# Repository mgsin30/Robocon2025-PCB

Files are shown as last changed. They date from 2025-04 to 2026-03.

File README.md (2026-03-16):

# Robocon2025-PCB
高専ロボコン2025のために開発した基板 <br>
各基板のファームウェアは [こちら](https://github.com/mgsin30/Robocon2025-Firmware)

## CAN Bus Hub
各基板を CAN バスで接続するためのハブ基板

## Converter Board
サーボモーターや LED テープなどのために電源電圧を降圧する基板

## GPIO Board
リミットスイッチやジャイロセンサー、その他 GPIO を使うための基板

## Motor Driver
ブラシ付きモーター用のモータードライバー

## Power Board
電源電圧の監視や非常停止の管理などを行う電源基板

## PWM Board
サーボモーターなどを使うための基板

## Remote Emergency Stop Board (TX)
遠隔非常停止の送信側基板

## Remote Emergency Stop Board (RX)
遠隔非常停止の受信側基板

## RoboMaster Board
ロボマスモーターを使うための基板

## Solenoid Driver
ソレノイドや電磁弁などを使うための基板

## USB-CAN Board
USB と CAN を変換する基板

## XT30 Hub
XT30 コネクタのハブ基板

## XT60 Hub
XT60 コネクタのハブ基板

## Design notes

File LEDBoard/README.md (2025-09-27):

# LED Board

LEDテープ WS2812B を光らせるための基板

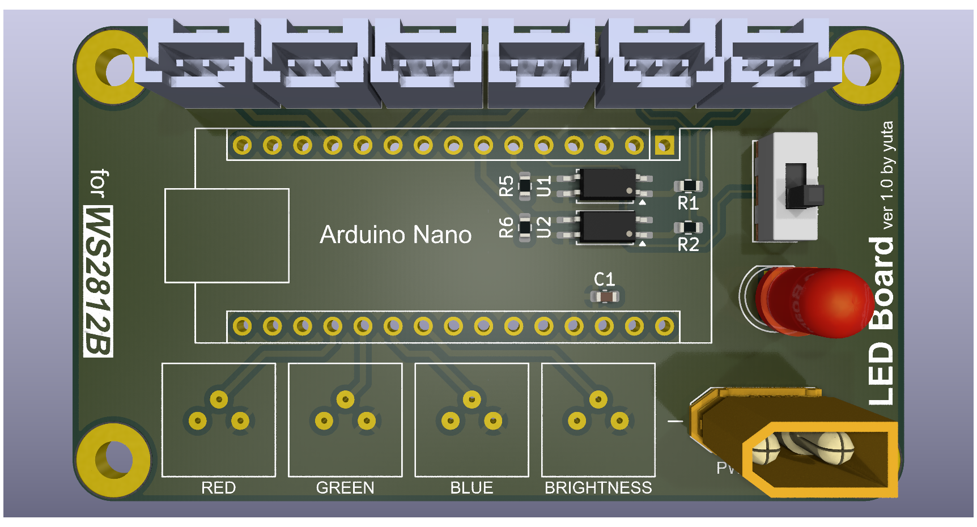
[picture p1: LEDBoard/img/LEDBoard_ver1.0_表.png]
表面

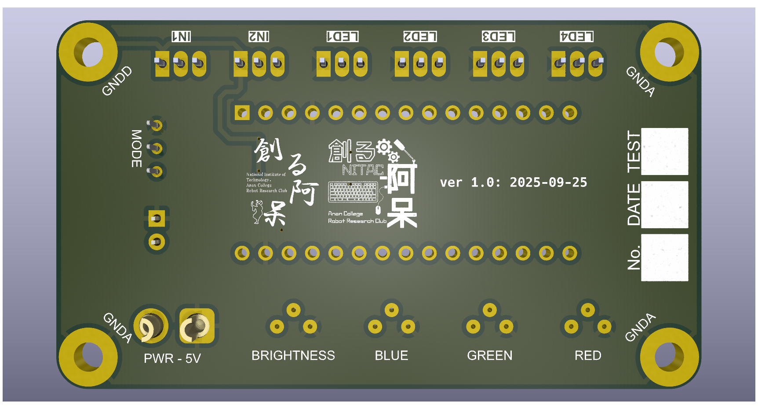
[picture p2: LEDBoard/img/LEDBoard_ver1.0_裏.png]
裏面


## 変更履歴

### ver1.0 (完成日：2025/09/25)
- 初回完成

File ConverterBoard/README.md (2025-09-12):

# Converter Board

電源電圧を各電圧に降圧するための基板

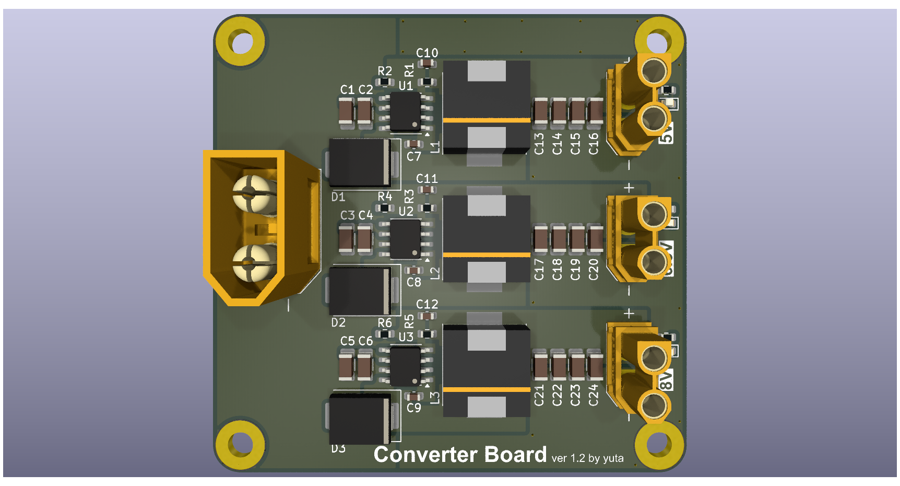
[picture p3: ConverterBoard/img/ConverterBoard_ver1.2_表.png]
表面

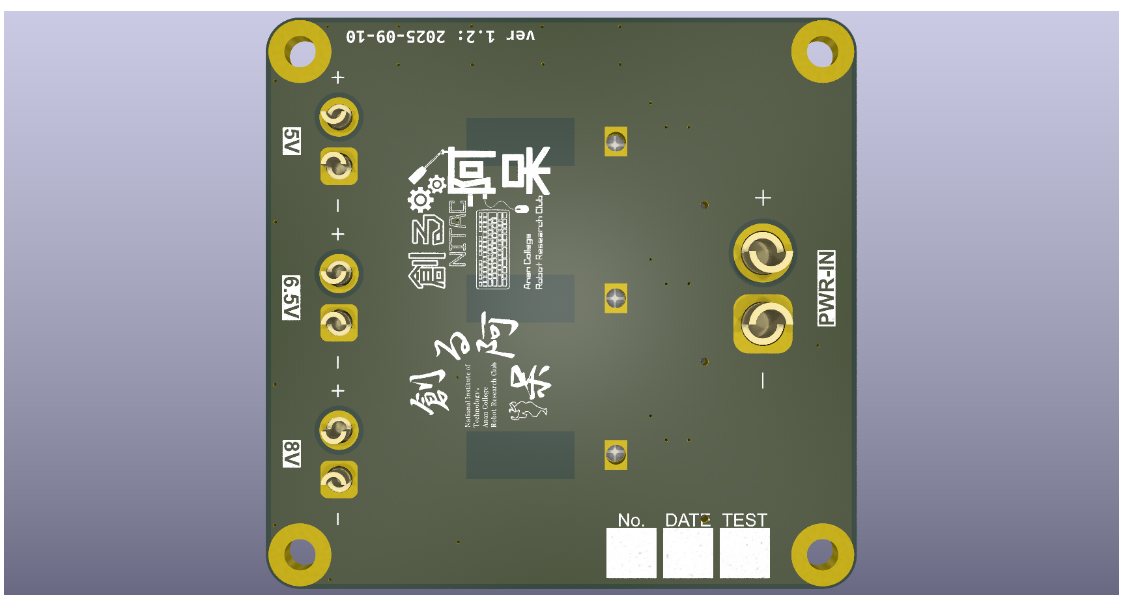
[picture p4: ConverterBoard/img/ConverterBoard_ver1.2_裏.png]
裏面


## 変更履歴

### ver1.0 (完成日：2025/05/31)
- 初回完成

### ver1.1 (完成日：2025/06/17)
- D1, D2, D3 のフットプリントを修正
- U1, U2, U3 のフットプリントを修正

### ver1.2 (完成日：2025/09/10)
- 12V出力を8V出力に変更
- 電源確認用LEDを追加
- 裏面のロゴの位置を微調整

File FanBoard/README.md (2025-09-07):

# Fan Board

空冷ファン用基板

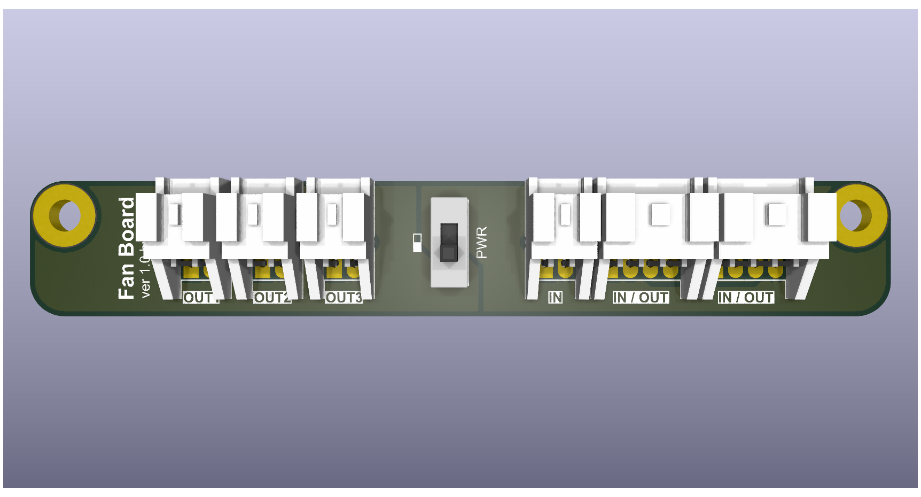
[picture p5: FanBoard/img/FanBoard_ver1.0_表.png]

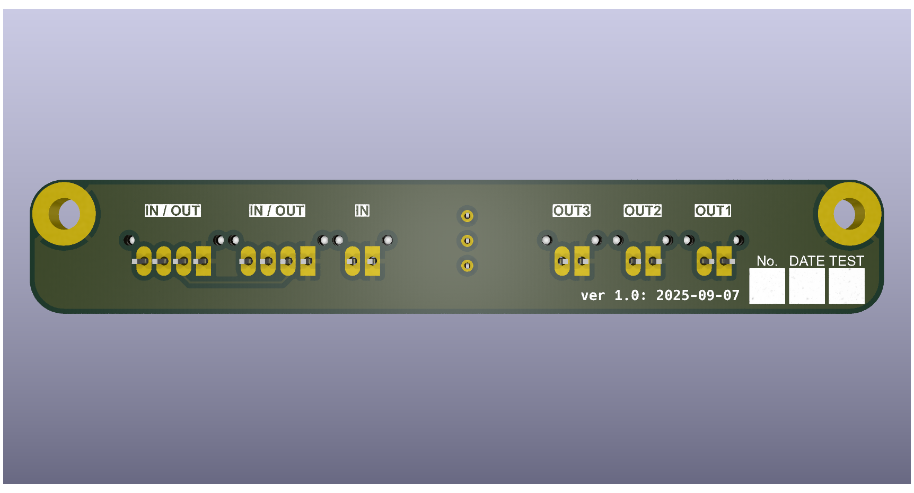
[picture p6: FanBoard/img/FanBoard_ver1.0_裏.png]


## 変更履歴

### ver1.0 (完成日：2025/09/07)
- 初回完成

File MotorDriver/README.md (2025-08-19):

# Motor Driver

ブラシ付きモーター用のモータードライバー

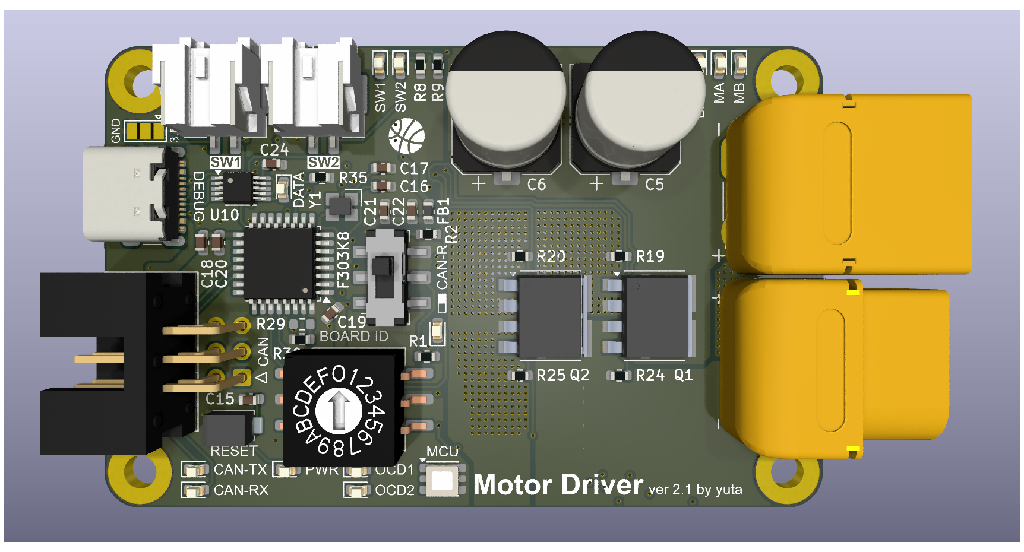
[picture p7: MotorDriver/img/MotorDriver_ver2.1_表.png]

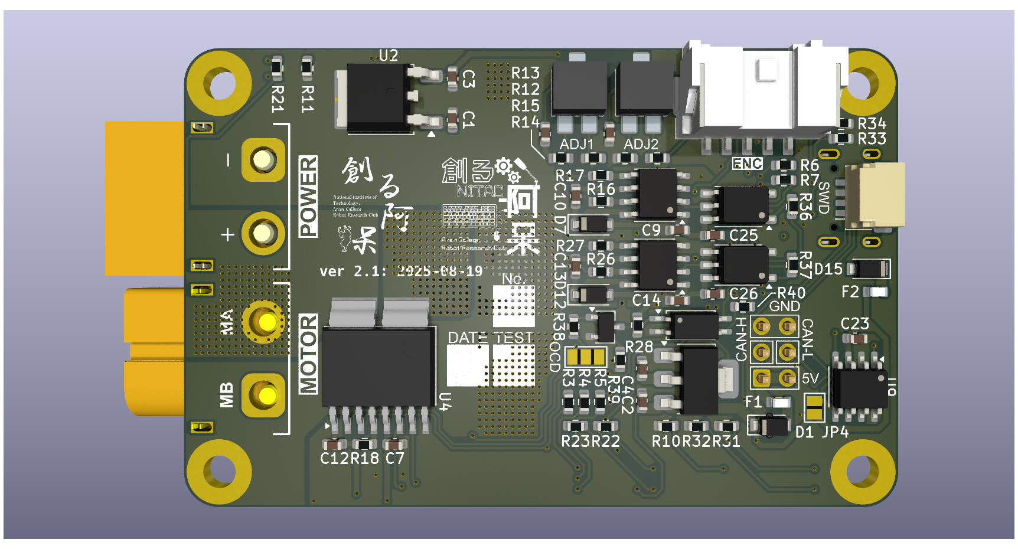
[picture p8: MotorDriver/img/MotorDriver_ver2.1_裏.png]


## 変更履歴

### ver1.0 (発注日：2025/02/24)
- 初回完成

### ver2.0 (完成日：2025/07/11)
- 小型化
- マイコンを搭載
- 他の基板に合わせて仕様を変更

### ver2.1 (完成日：2025/08/19)
- エンコーダー用のピンを変更
- MOSFETのフットプリントを修正
- C23のシルクを追加

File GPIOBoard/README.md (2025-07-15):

# GPIO Board

リミットスイッチや IMU を接続したり、GPIO を利用したりするための基板

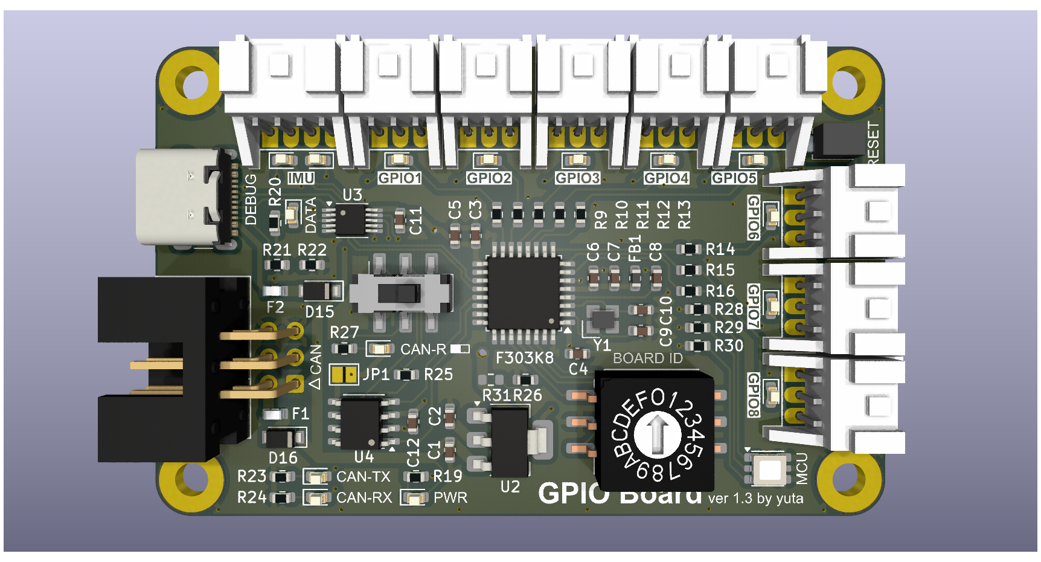
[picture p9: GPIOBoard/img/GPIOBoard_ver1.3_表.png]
表面

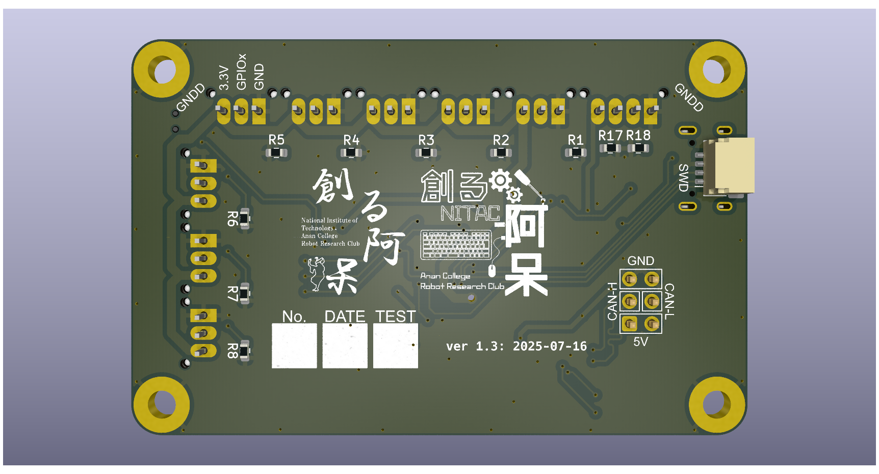
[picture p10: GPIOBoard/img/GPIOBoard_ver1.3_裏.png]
裏面


## 変更履歴

### ver1.0 (発注日：2025/03/10)
- 初回完成

### ver1.1 (発注日：2025/04/12)
- 三端子レギュレーターの型番を変更
- ショットキーバリアダイオードの型番を変更
- 各LEDの型番を変更
- 電源確認用LEDの場所を変更
- RGBLEDを追加
- 終端抵抗接続用スイッチの型番を変更
- 終端抵抗接続確認用のLEDを追加
- シルクを微調整
- 水晶発振子のフットプリントを修正

### ver1.2 (発注日：2025/07/01)
- USB-Cコネクタの位置を微調整
- 基板下部の取付穴を通常の穴に変更

### ver1.3 (発注日：2025/07/16)
- USBのCCピンが未配線だったのを修正
- フットプリントを更新

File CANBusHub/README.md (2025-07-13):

# CAN Bus Hub

各基板と CANバス を接続する基板

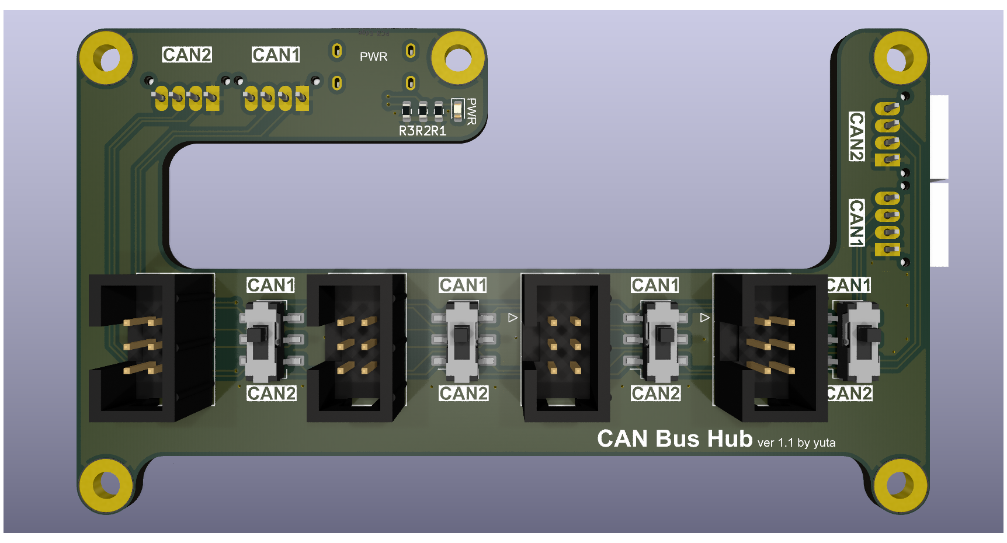
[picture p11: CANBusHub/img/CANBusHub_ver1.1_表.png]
表面

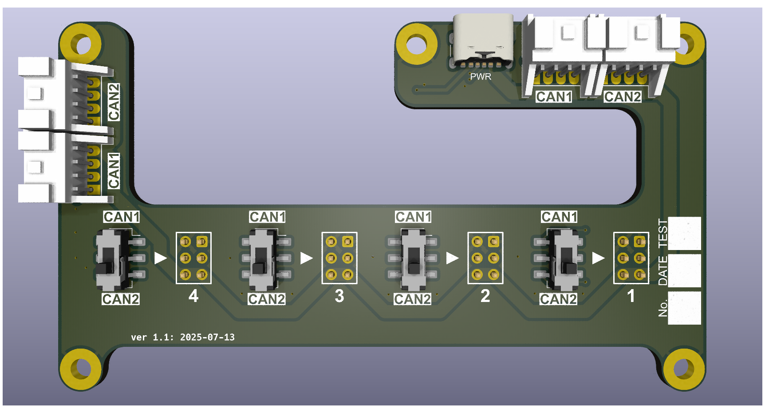
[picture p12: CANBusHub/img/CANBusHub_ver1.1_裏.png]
裏面


## 変更履歴

### ver1.0 (完成日：2025/05/30)
- 初回完成

### ver1.1 (完成日：2025/07/13)
- 基板接続用コネクタとCANバス切替用スイッチの位置を変更
- CAN用コネクタの位置を変更
- 裏面にシルクスクリーンを追加

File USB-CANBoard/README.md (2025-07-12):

# USB-CAN Board

USB と CAN の変換基板

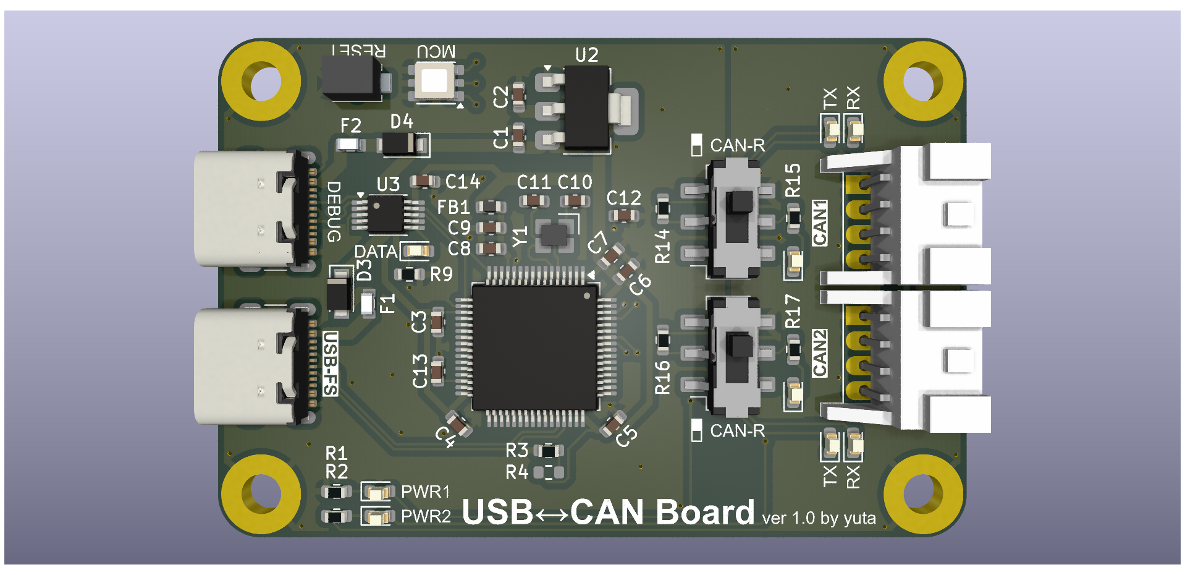
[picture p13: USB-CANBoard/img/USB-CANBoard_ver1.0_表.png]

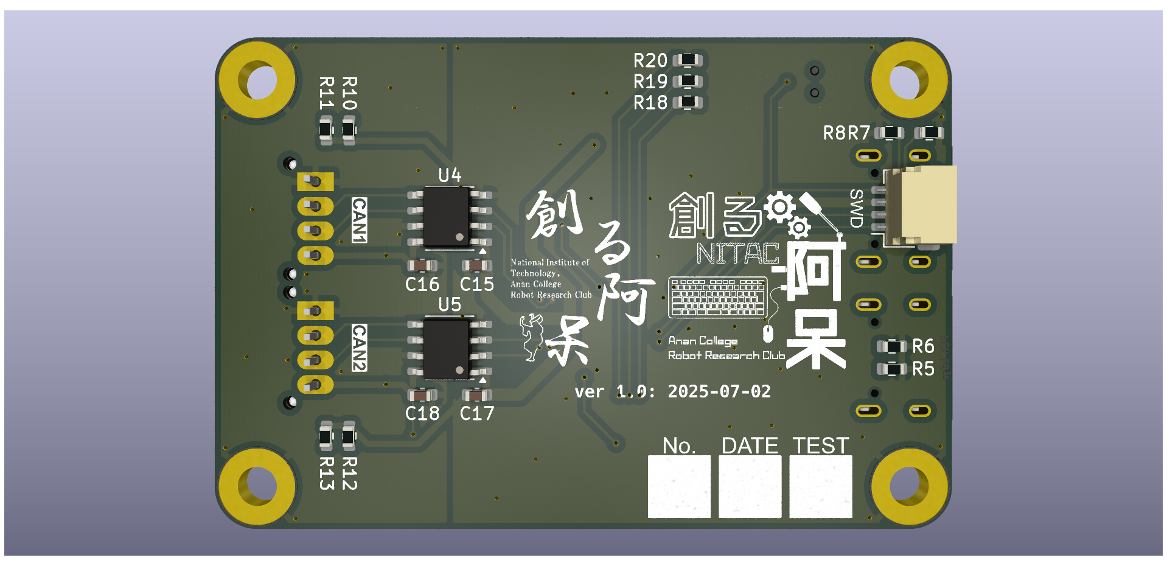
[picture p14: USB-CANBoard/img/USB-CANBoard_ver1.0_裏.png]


## 変更履歴

### ver1.0 (完成日：2025/07/02)
- 初回完成

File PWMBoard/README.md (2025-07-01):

# PWM Board

PWM を出力し、サーボモーターや ESC、LEDテープを接続するための基板

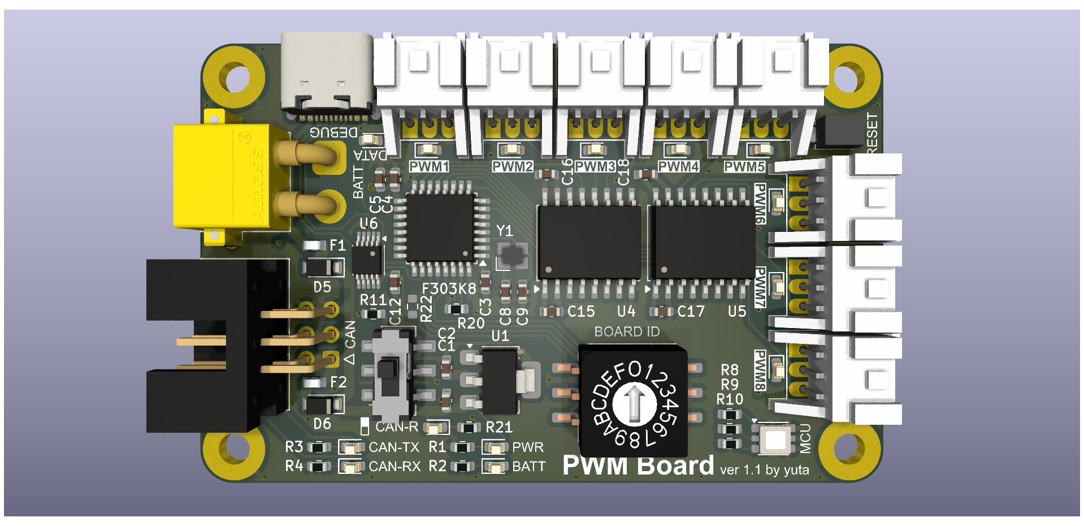
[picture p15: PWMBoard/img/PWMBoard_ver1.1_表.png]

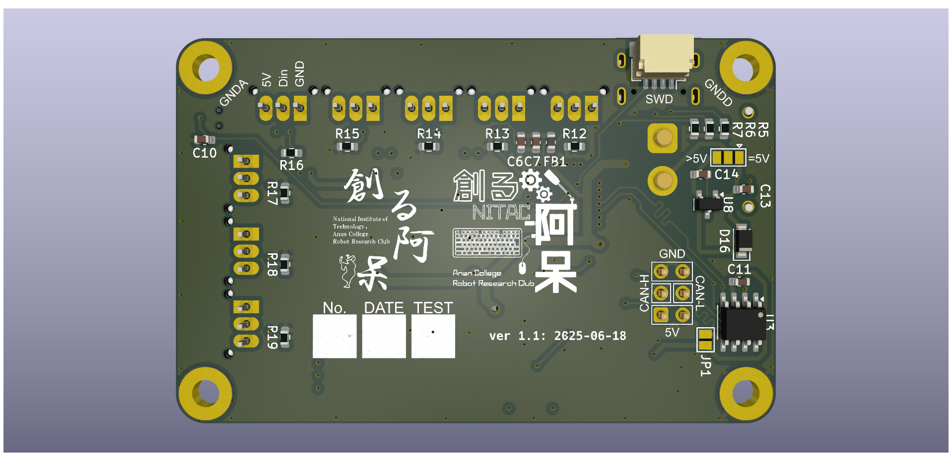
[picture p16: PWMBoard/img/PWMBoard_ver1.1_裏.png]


## 変更履歴

### ver1.0 (発注日：2025/04/12)
- 初回完成

### ver1.1 (完成日：2025/06/18)
- 電源コネクタの接続が逆になっていたのを修正
- 基板下部の取付穴を通常の穴に変更

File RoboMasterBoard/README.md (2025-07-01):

# RoboMaster Board

ロボマスモーターを制御するための基板

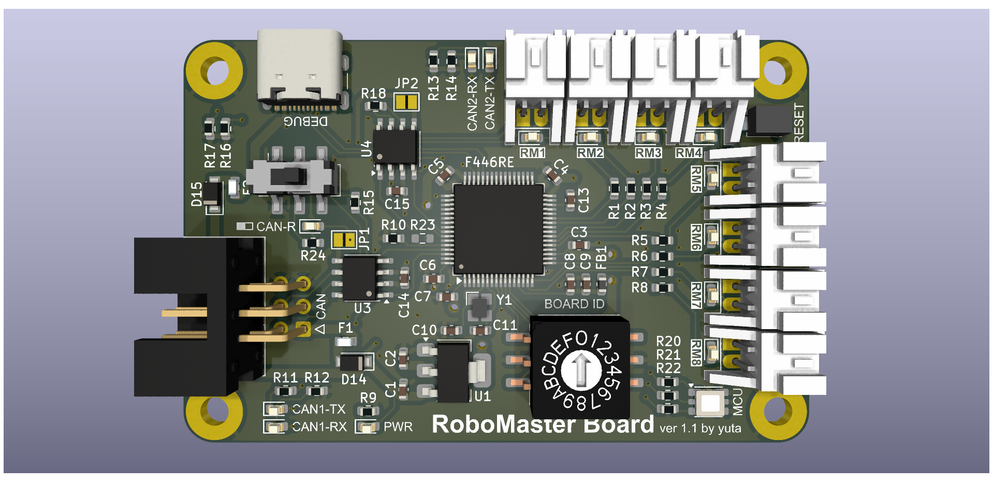
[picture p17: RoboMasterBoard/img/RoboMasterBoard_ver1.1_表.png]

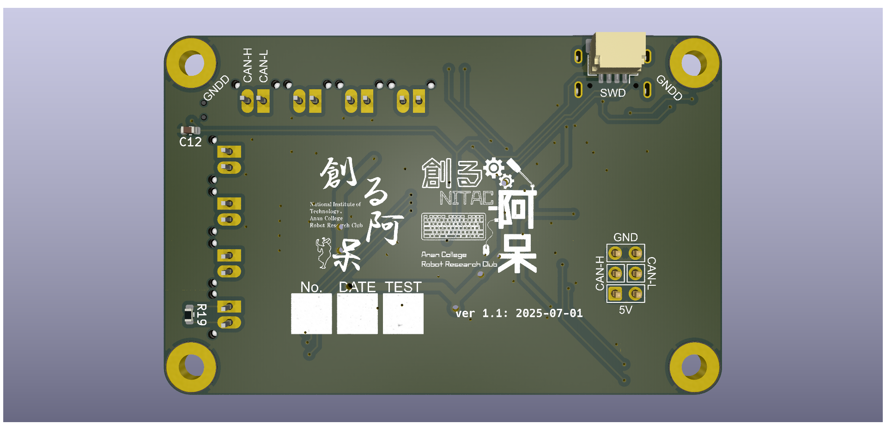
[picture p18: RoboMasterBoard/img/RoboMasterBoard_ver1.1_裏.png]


## 変更履歴

### ver1.0 (発注日：2025/04/12)
- 初回完成

### ver1.1 (発注日：2025/07/01)
- 未接続の箇所を修正
- 水晶発振子の型番を変更
- U2 のシルクの向きを変更
- 基板下部の取付穴を通常の穴に変更

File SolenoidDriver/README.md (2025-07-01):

# Solenoid Driver

ソレノイドやソレノイドバルブを制御するための基板

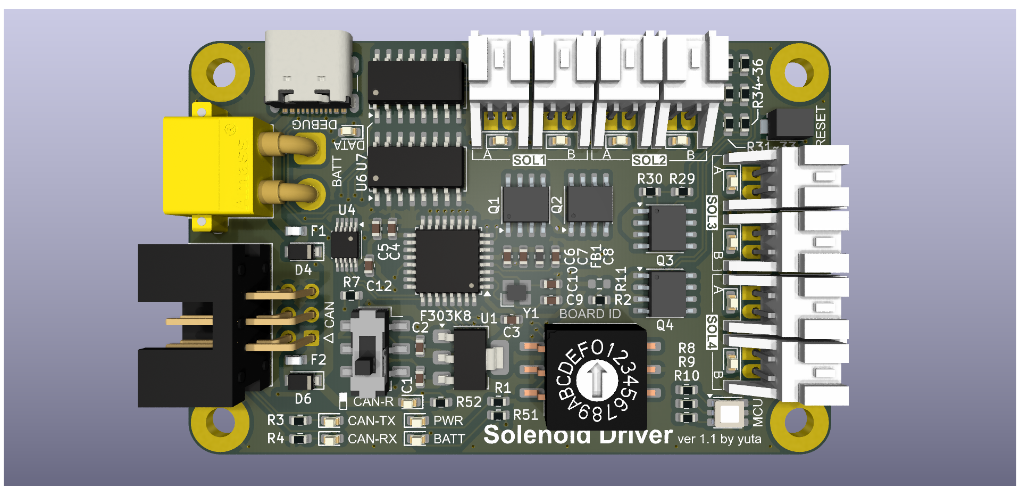
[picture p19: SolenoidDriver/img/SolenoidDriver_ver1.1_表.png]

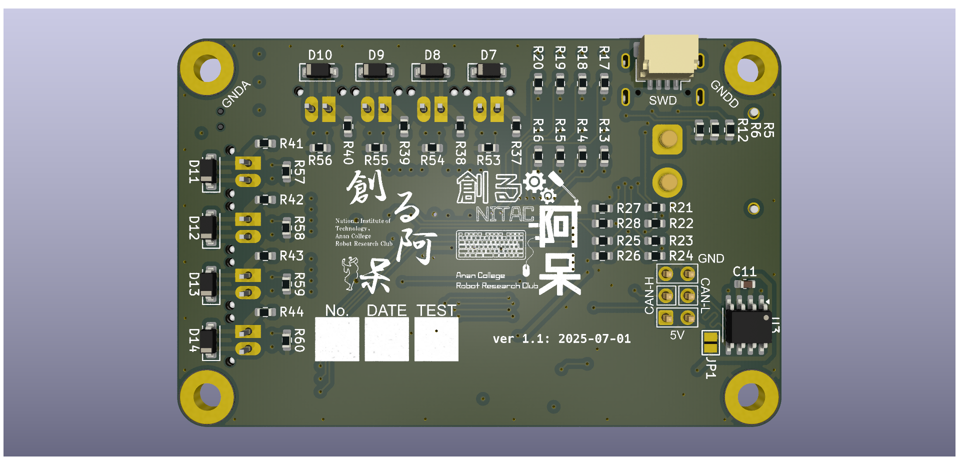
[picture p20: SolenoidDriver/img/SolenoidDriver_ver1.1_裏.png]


## 変更履歴

### ver1.0 (発注日：2025/04/12)
- 初回完成

### ver1.1 (発注日：2025/07/01)
- 電源コネクタの接続が逆になっていたのを修正
- ソレノイド接続部に電流制限抵抗を追加
- 基板下部の取付穴を通常の穴に変更
- コネクタ部のシルクのサイズを微調整

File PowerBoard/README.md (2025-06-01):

# Power Board

電源の監視、制御電源の生成、非常停止などを行う電源基板

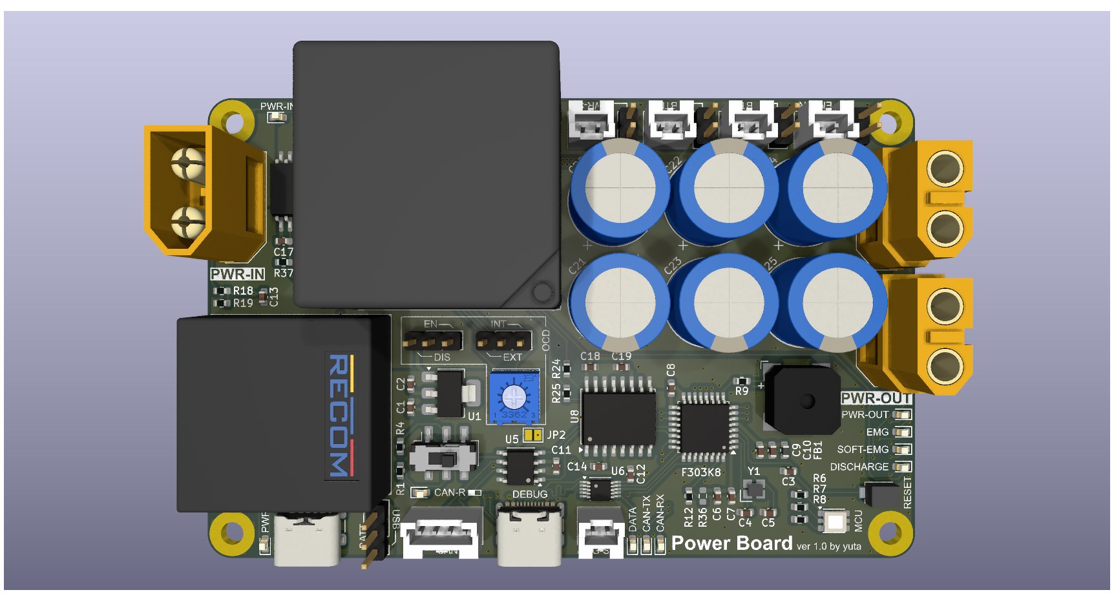
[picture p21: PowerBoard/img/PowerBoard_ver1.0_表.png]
表面

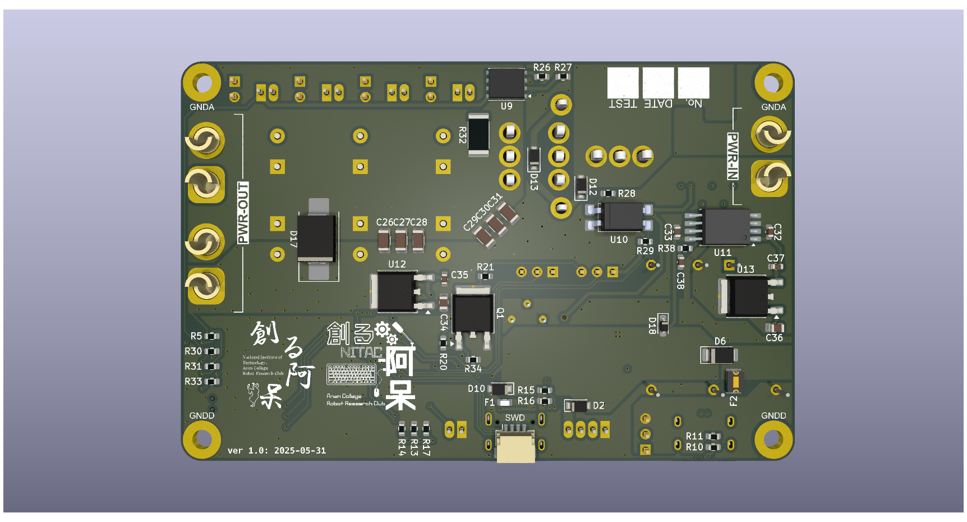
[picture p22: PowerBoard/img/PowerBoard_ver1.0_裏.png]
裏面


## 変更履歴

### ver1.0 (完成日：2025/05/31)
- 初回完成

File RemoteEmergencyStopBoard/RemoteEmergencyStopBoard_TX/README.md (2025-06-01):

# Remote Emergency Stop Board (TX)

遠隔非常停止の送信基板

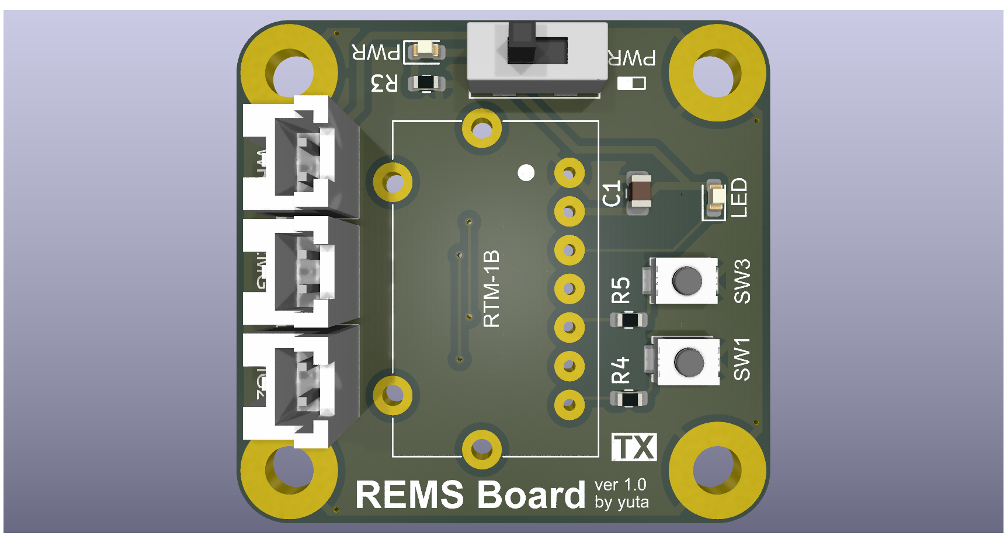
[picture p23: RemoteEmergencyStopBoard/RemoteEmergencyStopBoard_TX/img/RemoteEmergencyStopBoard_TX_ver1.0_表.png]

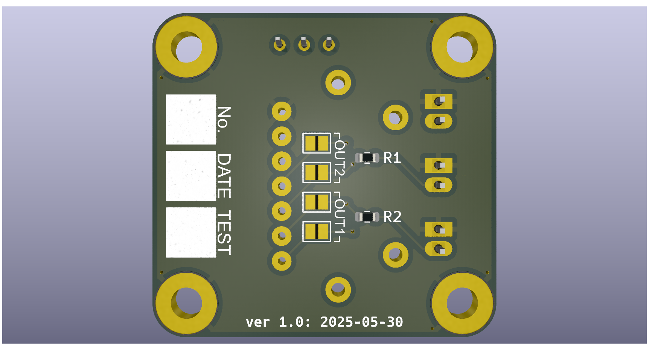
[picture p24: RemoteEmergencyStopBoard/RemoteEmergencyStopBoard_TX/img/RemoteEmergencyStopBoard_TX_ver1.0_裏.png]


## 変更履歴

### ver1.0 (完成日：2025/05/30)
- 初回完成

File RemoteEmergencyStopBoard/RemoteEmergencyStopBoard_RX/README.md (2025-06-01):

# Remote Emergency Stop Board (RX)

遠隔非常停止の受信基板

表面
表面

## 変更履歴

### ver1.0 (完成日：2025/05/30)
- 初回完成

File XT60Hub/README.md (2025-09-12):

# XT60 Hub

1つの入力を5つの出力に分岐させる XT60 コネクタのハブ

表面
表面

## 変更履歴

### ver1.0 (発注日：2025/04/12)
- 初回完成

### ver1.1 (完成日：2025/09/10)
- 基板の外形を編集
- 基板取付穴の位置を微調整

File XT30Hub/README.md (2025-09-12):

# XT30 Hub

1つの入力を5つの出力に分岐させる XT30 コネクタのハブ

表面
表面

## 変更履歴

### ver1.0 (発注日：2025/04/12)
- 初回完成

### ver1.1 (完成日：2025/09/10)
- 基板の外形を変更
- 基板取付穴の位置を微調整

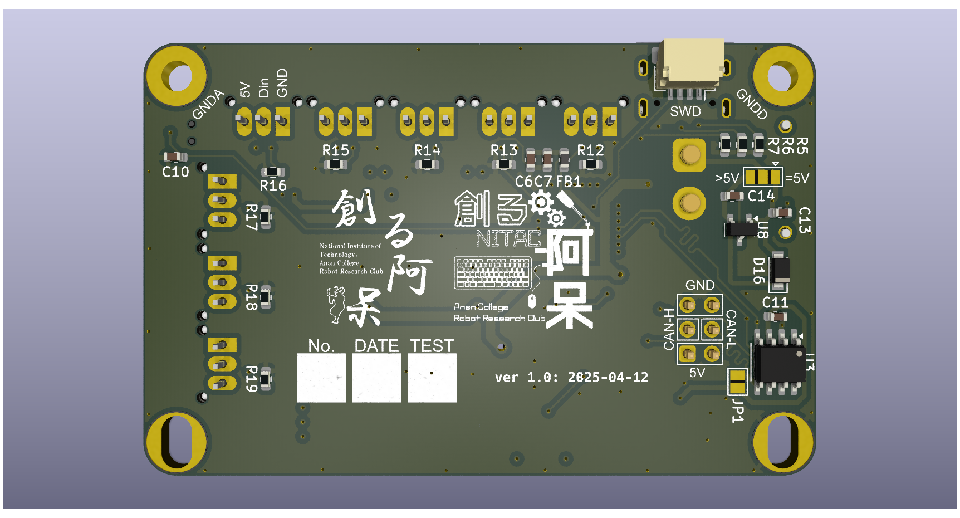
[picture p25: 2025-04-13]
PWMBoard/img/PWMBoard_ver1.0_裏.png

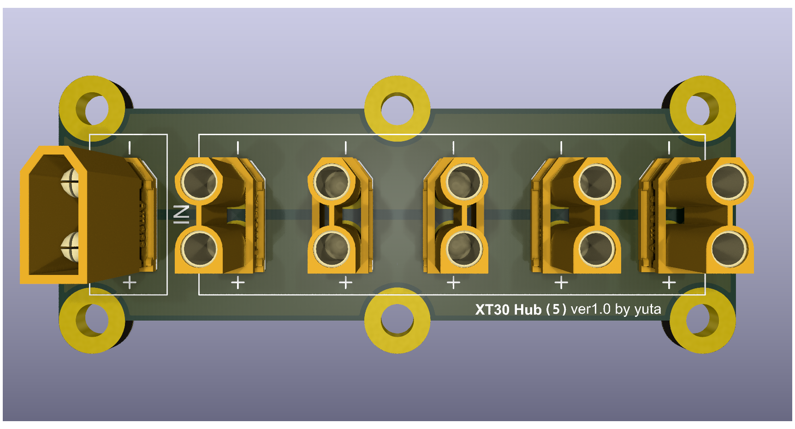
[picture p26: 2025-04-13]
XT30Hub/img/XT30Hub_ver1.0_表.png

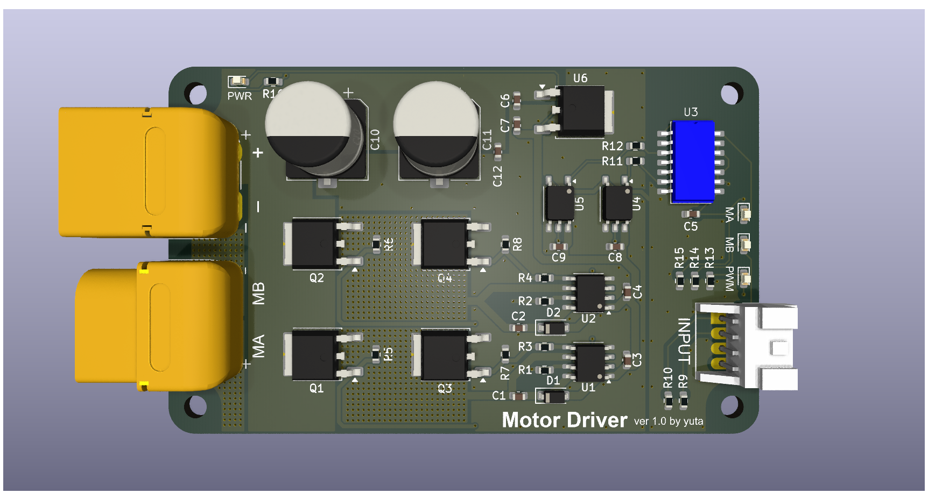
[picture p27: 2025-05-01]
MotorDriver/img/MotorDriver_ver1.0_表.png

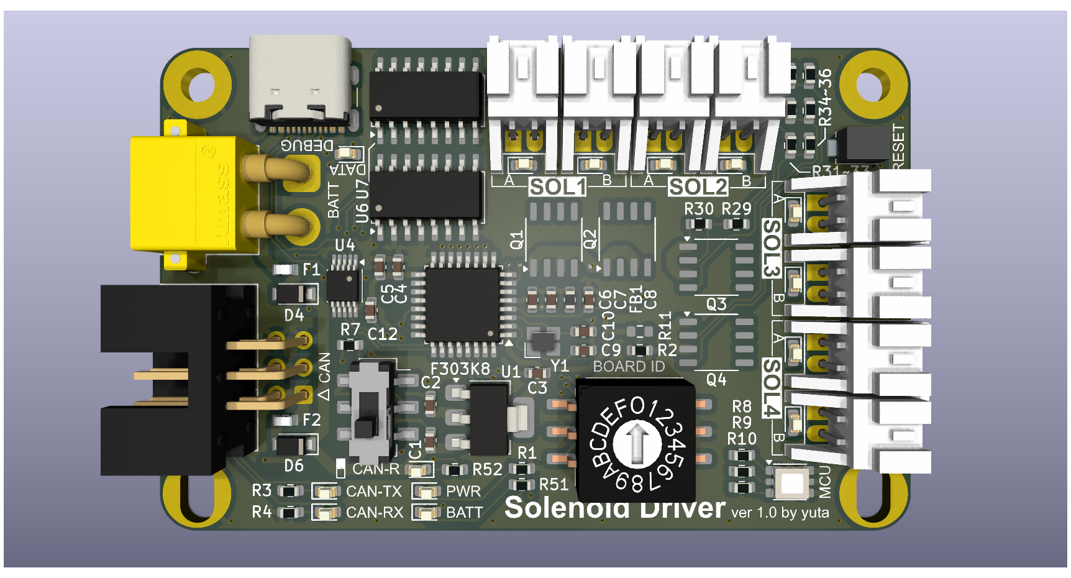
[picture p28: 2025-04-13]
SolenoidDriver/img/SolenoidDriver_ver1.0_表.png

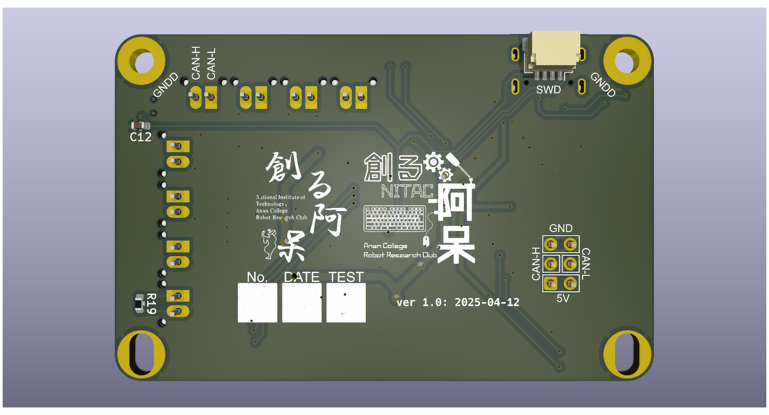
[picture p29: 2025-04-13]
RoboMasterBoard/img/RoboMasterBoard_ver1.0_裏.png

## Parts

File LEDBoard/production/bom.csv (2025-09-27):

Designator | Footprint | Quantity | Value | LCSC Part #
A1 | Arduino_Nano | 1 | Arduino_Nano_v3.x
C1 | 0603 | 1 | 0.1u
D1 | LED_D5.0mm | 1 | LED
J1 | AMASS_XT30U-M_1x02_P5.0mm_Vertical | 1 | PWR
J2 | PAコネクタ(3ピントップ型) | 1 | LED1
J3 | PAコネクタ(3ピントップ型) | 1 | LED2
J4 | PAコネクタ(3ピントップ型) | 1 | LED3
J5 | PAコネクタ(3ピントップ型) | 1 | LED4
J6 | PAコネクタ(3ピントップ型) | 1 | IN1
J7 | PAコネクタ(3ピントップ型) | 1 | IN2
R1, R2 | 0603 | 2 | R
R5, R6 | 0603 | 2 | 10k
RV1 | TSR-3386K | 1 | Red
RV2 | TSR-3386K | 1 | Green
RV3 | TSR-3386K | 1 | Blue
RV4 | TSR-3386K | 1 | Brightness
SW1 | SS-12D00G3 | 1 | MODE
U1, U2 | SOIC-4_4.55x2.6mm_P1.27mm | 2 | TLP291

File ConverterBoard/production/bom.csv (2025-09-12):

Designator | Footprint | Quantity | Value | LCSC Part #
C1, C2, C3, C4, C5, C6 | 1206 | 6 | 4.7u
C10, C11, C12 | 0603 | 3 | 82p
C13, C14, C15, C16, C17, C18, C19, C20, C21, C22, C23, C24 | 1206 | 12 | 22u
C7, C8, C9 | 0603 | 3 | 10n
D1, D2, D3 | D_SMC | 3 | D_Schottky
D4 | 0603 | 1 | BATT
D5 | 0603 | 1 | 5V
D6 | 0603 | 1 | 6.5V
D7 | 0603 | 1 | 12V
J1 | AMASS_XT60-M_1x02_P7.20mm_Vertical | 1 | PWR_IN
J2 | AMASS_XT30U-F_1x02_P5.0mm_Vertical | 1 | PWR_OUT1
J3 | AMASS_XT30U-F_1x02_P5.0mm_Vertical | 1 | PWR_OUT2
J4 | AMASS_XT30U-F_1x02_P5.0mm_Vertical | 1 | PWR_OUT3
L1 | L_Taiyo-Yuden_NR-10050_9.8x10.0mm_HandSoldering | 1 | 15u
L2, L3 | L_Taiyo-Yuden_NR-10050_9.8x10.0mm_HandSoldering | 2 | 22u
R1, R3, R5 | 0603 | 3 | 100k
R10 | 0603 | 1 | 500
R2 | 0603 | 1 | 31.6k
R4 | 0603 | 1 | 22.9k
R6 | 0603 | 1 | 18k
R7 | 0603 | 1 | 1.5k
R8 | 0603 | 1 | 240
R9 | 0603 | 1 | 390
U1, U2, U3 | SOIC-8-1EP_3.9x4.9mm_P1.27mm_EP2.29x3mm_Handsoldering | 3 | RT6285

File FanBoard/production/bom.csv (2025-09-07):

Designator | Footprint | Quantity | Value | LCSC Part #
J1 | PAコネクタ(4ピンサイド型) | 1 | Vin / CAN IN
J2 | PAコネクタ(2ピンサイド型) | 1 | Vin
J3 | PAコネクタ(4ピンサイド型) | 1 | CAN OUT
J4 | PAコネクタ(2ピンサイド型) | 1 | OUT1
J5 | PAコネクタ(2ピンサイド型) | 1 | OUT2
J6 | PAコネクタ(2ピンサイド型) | 1 | OUT3
SW1 | SS-12D00G3 | 1 | PWR

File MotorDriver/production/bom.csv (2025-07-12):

Designator | Footprint | Quantity | Value | LCSC Part #
C1 | 0603 | 1 | 0.33u
C10, C13 | 0603 | 2 | 2.5u
C11, C12, C8 | 0603 | 3 | 1000p
C14, C15, C19, C20, C21, C23, C24, C25, C26, C3, C7, C9 | 0603 | 12 | 0.1u
C16, C17 | 0603 | 2 | 15p
C18, C2, C4 | 0603 | 3 | 4.7u
C22 | 0603 | 1 | 1u
C5, C6 | CP_Elec_10x10.5 | 2 | 330u
D1, D15 | Nexperia_CFP3_SOD-123W | 2 | D
D10 | 0603 | 1 | OCD1
D11 | 0603 | 1 | OCD2
D12, D7 | D_SOD-123 | 2 | D_Schottky
D13 | 0603 | 1 | CAN_TX
D14 | 0603 | 1 | CAN_RX
D16 | 0603 | 1 | DATA
D2 | 0603 | 1 | CAN_R
D3 | 0603 | 1 | SW2
D4 | 0603 | 1 | SW1
D5 | 0603 | 1 | PWR
D6 | 0603 | 1 | BATT
D8 | 0603 | 1 | MA
D9 | 0603 | 1 | MB
F1, F2 | MF-FSMF | 2 | Polyfuse
FB1 | 0603 | 1 | FerriteBead
J1 | IDC-Header_2x03_P2.54mm_Horizontal | 1 | CAN
J2 | SM05B-PASS-TBx | 1 | ENC
J3 | SM02B-PASS-TBx | 1 | SW1
J4 | SM02B-PASS-TBx | 1 | SW2
J5 | XT60PW-M_Horizontal | 1 | VIN
J6 | XT60PW-F_Horizontal | 1 | Motor
J7 | JST_SH_SM04B-SRSS-TB_1x04-1MP_P1.00mm_Horizontal | 1 | SWD
J8 | USB_C_Receptacle_GCT_USB4105-xx-A_16P_TopMnt_Horizontal | 1 | Debug
Q1, Q2 | Vishay_PowerPAK_8x8L_Dual | 2 | Q_NMOS
Q3 | TSOT-23 | 1 | Q_NMOS_GSD
R1, R22, R23 | 0603 | 3 | 420
R10 | 0603 | 1 | 430
R11, R18 | 0603 | 2 | 1.5k
R12 | 0603 | 1 | 13k
R13 | 0603 | 1 | 2.4k
R14 | 0603 | 1 | 18k
R15 | 0603 | 1 | 3k
R16, R17, R26, R27, R8, R9 | 0603 | 6 | 80
R19, R20, R24, R25, R29, R30, R39, R40 | 0603 | 8 | 10k
R2 | 0603 | 1 | 120
R21 | 0603 | 1 | 3.7k
R28 | 0603 | 1 | 1k
R3, R31, R32, R35 | 0603 | 4 | 100
R33, R34 | 0603 | 2 | 5.1k
R36, R37 | 0603 | 2 | 350
R38 | 0603 | 1 | 660
R4 | 0603 | 1 | 600
R5 | 0603 | 1 | 300
R6, R7 | 0603 | 2 | 330
RV1, RV2 | ST-4ETB103 | 2 | 10k
SW1 | SLW | 1 | CAN_R
SW2 | RDS-1055-SMT | 1 | SW_Coded
SW3 | TVAF06-A020B-R | 1 | RESET
U1 | LED_ROHM_SMLVN6 | 1 | LED_GRB
U10 | MSOP-10_3x3mm_P0.5mm | 1 | CH340E
U11, U12 | SO-5-6_4.55x3.7mm_P1.27mm | 2 | TLP2348
U2 | TO-252-2 | 1 | NJM7812SDL1
U3 | SOT-223-3_TabPin2 | 1 | TLV1117-33
U4 | CZ3A | 1 | CZ-3A05
U5, U6 | SOIC-8_3.9x4.9mm_P1.27mm | 2 | IR2302
U7 | SOIC-4_4.55x2.6mm_P1.27mm | 1 | TLP293
U8 | LQFP-32_7x7mm_P0.8mm | 1 | STM32F303K8Tx
U9 | SOIC-8_3.9x4.9mm_P1.27mm | 1 | MCP2561/2FD
Y1 | XRCGB | 1 | Crystal_GND2

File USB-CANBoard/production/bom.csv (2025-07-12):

Designator | Footprint | Quantity | Value | LCSC Part #
C1, C13, C2, C7 | 0603 | 4 | 4.7u
C10, C11 | 0603 | 2 | 12p
C12, C14, C15, C16, C17, C18, C3, C4, C5, C6, C8 | 0603 | 11 | 0.1u
C9 | 0603 | 1 | 1u
D1, D2, D5 | 0603 | 3 | LED
D10, D11 | 0603 | 2 | CAN_R
D3, D4 | Nexperia_CFP3_SOD-123W | 2 | D
D6 | 0603 | 1 | CAN1_TX
D7 | 0603 | 1 | CAN1_RX
D8 | 0603 | 1 | CAN2_TX
D9 | 0603 | 1 | CAN2_RX
F1, F2 | MF-FSMF | 2 | Polyfuse
FB1 | 0603 | 1 | FerriteBead
J1 | USB_C_Receptacle_GCT_USB4105-xx-A_16P_TopMnt_Horizontal | 1 | USB_FS
J2 | USB_C_Receptacle_GCT_USB4105-xx-A_16P_TopMnt_Horizontal | 1 | DEBUG
J3 | PAコネクタ(4ピンサイド型) | 1 | CAN1
J4 | PAコネクタ(4ピンサイド型) | 1 | CAN2
J5 | JST_SH_SM04B-SRSS-TB_1x04-1MP_P1.00mm_Horizontal | 1 | SWD
R1, R2 | 0603 | 2 | 430
R10, R11, R12, R13, R15, R17, R9 | 0603 | 7 | R
R14, R16 | 0603 | 2 | 120
R18 | 0603 | 1 | 100
R19 | 0603 | 1 | 600
R20 | 0603 | 1 | 300
R3, R4 | 0603 | 2 | 10k
R5, R6, R7, R8 | 0603 | 4 | 5.1k
SW1 | TVAF06-A020B-R | 1 | RESET
SW2, SW3 | SLW | 2 | CAN_R
U1 | LQFP-64_10x10mm_P0.5mm | 1 | STM32F446RETx
U2 | SOT-223-3_TabPin2 | 1 | TLV1117-33
U3 | MSOP-10_3x3mm_P0.5mm | 1 | CH340E
U4, U5 | SOIC-8_3.9x4.9mm_P1.27mm | 2 | ISO1044BD
U6 | LED_ROHM_SMLVN6 | 1 | LED_GRB
Y1 | XRCGB | 1 | 26MHz

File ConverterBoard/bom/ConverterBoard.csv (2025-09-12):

Reference | Value | Name | URL | Price | Qty
C1,C2,C3,C4,C5,C6 | 4.7u | GCJ31CC71E106MA15L | https://www.digikey.jp/ja/products/detail/murata-electronics/GCJ31CC71E106MA15L/10694168 | 107 | 6
C7,C8,C9 | 10n | GCM1885C1H103JA16D | https://www.digikey.jp/ja/products/detail/murata-electronics/GCM1885C1H103JA16D/13402328 | 26 | 3
C10,C11,C12 | 82p | GCM1885C2A820JA16D | https://www.digikey.jp/ja/products/detail/murata-electronics/GCM1885C2A820JA16D/2591816 | 15 | 3
C13,C14,C15,C16,C17,C18,C19,C20,C21,C22,C23,C24 | 22u | CL31A226KAHNNNE | https://www.digikey.jp/ja/products/detail/samsung-electro-mechanics/CL31A226KAHNNNE/3888705 | 21 | 12
D1,D2,D3 | D_Schottky | B550C-13-F | https://www.digikey.jp/ja/products/detail/diodes-incorporated/B550C-13-F/768772 | 99 | 3
D4,D5,D6,D7 | 12V,5V,6.5V,BATT | SML-D12U8WT86 | https://www.digikey.jp/ja/products/detail/rohm-semiconductor/SML-D12U8WT86/1641799 | 30 | 4
J1 | PWR_IN | XT60U-M | https://akizukidenshi.com/catalog/g/g117953/ | 60 | 1
J2,J3,J4 | PWR_OUT1,PWR_OUT2,PWR_OUT3 | XT30U-F | https://akizukidenshi.com/catalog/g/g117950/ | 50 | 3
L1 | 15u | NR10050T150M | https://www.digikey.jp/ja/products/detail/taiyo-yuden/NR10050T150M/1171798 | 103 | 1
L2,L3 | 22u | NR10050T220M | https://www.digikey.jp/ja/products/detail/taiyo-yuden/NR10050T220M/1007973 | 103 | 2
R1,R3,R5 | 100k | RN73H1JTTD1003B25 | https://www.digikey.jp/ja/products/detail/koa-speer-electronics-inc/RN73H1JTTD1003B25/10675246 | 15 | 3
R2 | 31.6k | RN73H1JTTD3162B25 | https://www.digikey.jp/ja/products/detail/koa-speer-electronics-inc/RN73H1JTTD3162B25/10683077 | 15 | 1
R4 | 22.9k | RN73R1JTTD2292B25 | https://www.digikey.jp/ja/products/detail/koa-speer-electronics-inc/RN73R1JTTD2292B25/10013006 | 15 | 1
R6 | 18k | RN73H1JTTD1802B25 | https://www.digikey.jp/ja/products/detail/koa-speer-electronics-inc/RN73H1JTTD1802B25/10688678 | 32 | 1
R7 | 1.5k | ESR03EZPJ152 | https://www.digikey.jp/ja/products/detail/rohm-semiconductor/ESR03EZPJ152/1983456 | 22 | 1
R8 | 240 | ESR03EZPJ241 | https://www.digikey.jp/ja/products/detail/rohm-semiconductor/ESR03EZPJ241/1762728 | 22 | 1
R9 | 390 | ESR03EZPD3900 | https://www.digikey.jp/ja/products/detail/rohm-semiconductor/ESR03EZPD3900/21326149 | 31 | 1
R10 | 500 | ESR03EZPF4990 | https://www.digikey.jp/ja/products/detail/rohm-semiconductor/ESR03EZPF4990/21819734 | 23 | 1
U1,U2,U3 | RT6285 | RT6285GSP | https://www.digikey.jp/ja/products/detail/richtek-usa-inc/RT6285GSP/16376754 | 241 | 3

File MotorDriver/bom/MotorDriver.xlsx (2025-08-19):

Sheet: MotorDriver
Reference | Value | URL | Name | Price | Qty | Total
C1 | 0.33u | https://www.digikey.jp/ja/products/detail/samsung-electro-mechanics/CL10A225KB8NNNC/10479006 | CL10A225KB8NNNC | 37 | 1 | 37
C2 | 4.7u | https://www.digikey.jp/ja/products/detail/murata-electronics/GRM188R60J226MEA0D/4280542 | GRM188R60J226MEA0D | 27 | 1 | 27 | *
C3,C7,C9,C14,C15,C19,C20,C21,C23,C24,C25,C26 | 0.1u | https://www.digikey.jp/ja/products/detail/murata-electronics/GCJ188R91H124KA01D/13401917 | GCJ188R91H124KA01D | 34 | 12 | 408 | *
C4,C18 | 4.7u | https://www.digikey.jp/ja/products/detail/murata-electronics/GRM188R60G106ME47D/702562 | GRM188R60G106ME47D | 18 | 2 | 36 | *
C5,C6 | 330u | https://akizukidenshi.com/catalog/g/g117278/ | 50TPV330M10X10.5 | 40 | 2 | 80
C8,C11,C12 | 1000p | https://www.digikey.jp/ja/products/detail/w%C3%BCrth-elektronik/885012006029/5453626 | 885012006029 | 15 | 3 | 45
C10,C13 | 2.5u | https://www.digikey.jp/ja/products/detail/samsung-electro-mechanics/CL10A226MO7JZNC/7320581 | CL10A226MO7JZNC | 90 | 2 | 180
C16,C17 | 15p | https://www.digikey.jp/ja/products/detail/murata-electronics/GCM1885C2A150JA16D/1765189 | GCM1885C2A150JA16D | 15 | 2 | 30 | *
C22 | 1u | https://www.digikey.jp/ja/products/detail/murata-electronics/GRM188D71H105ME01W/22528412 | GRM188D71H105ME01W | 44 | 1 | 44 | *
D1,D15 | D | https://www.digikey.jp/ja/products/detail/nexperia-usa-inc/PMEG3010ER-115/2119868 | PMEG3010ER,115 | 29 | 2 | 58 | *
D2,D3,D4,D8,D9,D10,D11 | CAN_R,MA,MB,OCD1,OCD2,SW1,SW2 | https://www.digikey.jp/ja/products/detail/rohm-semiconductor/SMLD12BN1WT86/9826162 | SMLD12BN1WT86 | 47 | 7 | 329 | *
D5 | PWR | https://www.digikey.jp/ja/products/detail/rohm-semiconductor/SML-D12D8WT86/1641796 | SML-D12D8WT86 | 29 | 1 | 29 | *
D6 | BATT | https://www.digikey.jp/ja/products/detail/rohm-semiconductor/SML-D12U8WT86/1641799 | SML-D12U8WT86 | 29 | 1 | 29 | *
D7,D12 | D_Schottky | https://akizukidenshi.com/catalog/g/g101398/ | RB160M-30TR | 15 | 2 | 30
D13,D14,D16 | CAN_RX,CAN_TX,DATA | https://www.digikey.jp/ja/products/detail/rohm-semiconductor/SML-D14MWT86A/9448204 | SML-D14MWT86A | 52 | 3 | 156 | *
F1,F2 | Polyfuse | https://akizukidenshi.com/catalog/g/g114311/ | MF-FSMF020X-2 | 20 | 2 | 40
FB1 | FerriteBead | https://www.digikey.jp/ja/products/detail/murata-electronics/BLM18KG601SN1D/1982766 | BLM18KG601SN1D | 15 | 1 | 15
J1 | CAN | https://eleshop.jp/shop/g/g7AB411/ | JS-1200R-06 | 62 | 1 | 62
J2 | ENC | https://www.digikey.jp/ja/products/detail/jst-sales-america-inc/SM05B-PASS-TBT/2773428 | SM05B-PASS-TBT | 116 | 1 | 116
J3,J4 | SW1,SW2 | https://www.digikey.jp/ja/products/detail/jst-sales-america-inc/SM02B-PASS-TBT/1788574 | SM02B-PASS-TBT | 84 | 2 | 168
J5 | VIN | https://akizukidenshi.com/catalog/g/g118156/ | XT60PW-M | 100 | 1 | 100
J6 | Motor | https://akizukidenshi.com/catalog/g/g118155/ | XT60PW-F | 100 | 1 | 100
J7 | SWD | https://www.digikey.jp/ja/products/detail/jst-sales-america-inc/SM04B-SRSS-TB/926710 | SM04B-SRSS-TB | 76 | 1 | 76 | *
J8 | Debug | https://akizukidenshi.com/catalog/g/g114356/ | 5077CR-16-SMC2-BK-TR | 110 | 1 | 110
Q1,Q2 | Q_NMOS | https://www.digikey.jp/ja/products/detail/vishay-siliconix/SQJQ906EL-T1-GE3/6708921 | SQJQ906EL-T1_GE3 | 442 | 2 | 884
Q3 | Q_NMOS_GSD | https://akizukidenshi.com/catalog/g/g104232/ | BSS138 | 4 | 1 | 4
R1,R10,R22,R23 | 420430 | https://www.digikey.jp/ja/products/detail/rohm-semiconductor/ESR03EZPJ431/4051257 | ESR03EZPJ431 | 22 | 4 | 88
R2 | 120 | https://www.digikey.jp/ja/products/detail/rohm-semiconductor/ESR03EZPJ121/1983454 | ESR03EZPJ121 | 22 | 1 | 22
R3,R31,R32,R35 | 100 | https://www.digikey.jp/ja/products/detail/rohm-semiconductor/ESR03EZPJ101/1983452 | ESR03EZPJ101 | 22 | 4 | 88
R4 | 600 | https://www.digikey.jp/ja/products/detail/rohm-semiconductor/ESR03EZPF5900/20506305 | ESR03EZPF5900 | 22 | 1 | 22
R5 | 300 | https://www.digikey.jp/ja/products/detail/rohm-semiconductor/ESR03EZPJ301/1762729 | ESR03EZPJ301 | 22 | 1 | 22
R6,R7 | 330 | https://www.digikey.jp/ja/products/detail/rohm-semiconductor/ESR03EZPJ331/1762730 | ESR03EZPJ331 | 22 | 2 | 44
R8,R9,R16,R17,R26,R27 | 80 | https://www.digikey.jp/ja/products/detail/rohm-semiconductor/ESR03EZPJ820/4051294 | ESR03EZPJ820 | 22 | 6 | 132
R11,R18 | 1.5k | https://www.digikey.jp/ja/products/detail/rohm-semiconductor/ESR03EZPJ152/1983456 | ESR03EZPJ152 | 22 | 2 | 44
R12 | 13k | https://www.digikey.jp/ja/products/detail/susumu/RG1608P-133-B-T5/1240478 | RG1608P-133-B-T5 | 15 | 1 | 15
R13 | 2.4k | https://www.digikey.jp/ja/products/detail/susumu/RG1608P-242-B-T5/1240526 | RG1608P-242-B-T5 | 18 | 1 | 18
R14 | 18k | https://www.digikey.jp/ja/products/detail/susumu/RG1608P-183-B-T5/1240502 | RG1608P-183-B-T5 | 15 | 1 | 15
R15 | 3k | https://www.digikey.jp/ja/products/detail/susumu/RG1608P-302-B-T5/1240549 | RG1608P-302-B-T5 | 15 | 1 | 15
R19,R20,R24,R25,R29,R30,R39,R40 | 10k | https://www.digikey.jp/ja/products/detail/rohm-semiconductor/ESR03EZPJ103/1762722 | ESR03EZPJ103 | 22 | 8 | 176
R21 | 3.7k | https://www.digikey.jp/ja/products/detail/koa-speer-electronics-inc/RN73R1JTTD3701B25/10016282 | RN73R1JTTD3701B25 | 15 | 1 | 15
R28 | 1k | https://www.digikey.jp/ja/products/detail/rohm-semiconductor/ESR03EZPJ102/1762721 | ESR03EZPJ102 | 22 | 1 | 22
R33,R34 | 5.1k | https://www.digikey.jp/ja/products/detail/rohm-semiconductor/ESR03EZPJ512/1762735 | ESR03EZPJ512 | 22 | 2 | 44
R36,R37 | 350 | https://www.digikey.jp/ja/products/detail/susumu/RR0816P-3480-D-53A/432510 | RR0816P-3480-D-53A | 15 | 2 | 30
R38 | 660 | https://www.digikey.jp/ja/products/detail/stackpole-electronics-inc/RMCF0603FT665R/1714186 | RMCF0603FT665R | 15 | 1 | 15
RV1,RV2 | 10k | https://www.digikey.jp/ja/products/detail/nidec-components-corporation/ST-4ETB103/738213 | ST-4ETB103 | 233 | 2 | 466
SW1 | CAN_R | https://www.digikey.jp/ja/products/detail/same-sky-formerly-cui-devices/SLW-913535-2A-SMT/21259974 | SLW-913535-2A-SMT | 87 | 1 | 87
SW2 | SW_Coded | https://www.digikey.jp/ja/products/detail/same-sky-formerly-cui-devices/RDS-16S-1055-SMT-TR/12424507 | RDS-16S-1055-SMT-TR | 458 | 1 | 458
SW3 | RESET | https://akizukidenshi.com/catalog/g/g114888/ | TVAF06-A020B-R | 22 | 1 | 22
U1 | LED_GRB | https://www.digikey.jp/ja/products/detail/rohm-semiconductor/SMLVN6RGB1W1/5053781 | SMLVN6RGB1W1 | 244 | 1 | 244
U2 | NJM7812SDL1 | https://akizukidenshi.com/catalog/g/g110978/ | NJM7812SDL1 | 50 | 1 | 50
U3 | TLV1117-33 | https://www.digikey.jp/ja/products/detail/texas-instruments/TLV1117-33CDCYR/1216718 | TLV1117-33CDCYR | 63 | 1 | 63
U4 | CZ-3A05 | https://www.digikey.jp/ja/products/detail/asahi-kasei-microdevices-akm/CZ3A05/11570592 | CZ3A05 | 897 | 1 | 897
U5,U6 | IR2302 | https://akizukidenshi.com/catalog/g/g115656/ | IR2302STRPBF | 260 | 2 | 520
U7 | TLP293 | https://akizukidenshi.com/catalog/g/g116783/ | TLP293(BLL-TPL,E(T | 24 | 1 | 24
U8 | STM32F303K8Tx | https://akizukidenshi.com/catalog/g/g110790/ | STM32F303K8T6 | 780 | 1 | 780
U9 | MCP2561/2FD | https://www.digikey.jp/ja/products/detail/microchip-technology/MCP2562FDT-E-SN/4860105 | MCP2562FDT-E/SN | 202 | 1 | 202
U10 | CH340E | https://akizukidenshi.com/catalog/g/g113543/ | CH340E | 90 | 1 | 90
U11,U12 | TLP2348 | https://akizukidenshi.com/catalog/g/g118361/ | TLP2348(V4-TPL,E(T | 80 | 2 | 160
Y1 | Crystal_GND2 | https://www.digikey.jp/ja/products/detail/murata-electronics/XRCGB32M000F1SADR0/21662918 | XRCGB32M000F1SADR0 | 52 | 1 | 52
 |  |  |  |  | 合計 | 8135 | 円
 |  |  |  |  | 実質 | 6258 | 円

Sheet: 印刷用
Reference | Name | URL
C1 | CL10A225KB8NNNC | https://www.digikey.jp/ja/products/detail/samsung-electro-mechanics/CL10A225KB8NNNC/10479006
C2 | GRM188R60J226MEA0D | https://www.digikey.jp/ja/products/detail/murata-electronics/GRM188R60J226MEA0D/4280542
C3,C7,C9,C14,C15,C19,C20,C21,C23,C24,C25,C26 | GCJ188R91H124KA01D | https://www.digikey.jp/ja/products/detail/murata-electronics/GCJ188R91H124KA01D/13401917
C4,C18 | GRM188R60G106ME47D | https://www.digikey.jp/ja/products/detail/murata-electronics/GRM188R60G106ME47D/702562
C5,C6 | 50TPV330M10X10.5 | https://akizukidenshi.com/catalog/g/g117278/
C8,C11,C12 | 885012006029 | https://www.digikey.jp/ja/products/detail/w%C3%BCrth-elektronik/885012006029/5453626
C10,C13 | CL10A226MO7JZNC | https://www.digikey.jp/ja/products/detail/samsung-electro-mechanics/CL10A226MO7JZNC/7320581
C16,C17 | GCM1885C2A150JA16D | https://www.digikey.jp/ja/products/detail/murata-electronics/GCM1885C2A150JA16D/1765189
C22 | GRM188D71H105ME01W | https://www.digikey.jp/ja/products/detail/murata-electronics/GRM188D71H105ME01W/22528412
D1,D15 | PMEG3010ER,115 | https://www.digikey.jp/ja/products/detail/nexperia-usa-inc/PMEG3010ER-115/2119868
D2,D3,D4,D8,D9,D10,D11 | SMLD12BN1WT86 | https://www.digikey.jp/ja/products/detail/rohm-semiconductor/SMLD12BN1WT86/9826162
D5 | SML-D12D8WT86 | https://www.digikey.jp/ja/products/detail/rohm-semiconductor/SML-D12D8WT86/1641796
D6 | SML-D12U8WT86 | https://www.digikey.jp/ja/products/detail/rohm-semiconductor/SML-D12U8WT86/1641799
D7,D12 | RB160M-30TR | https://akizukidenshi.com/catalog/g/g101398/
D13,D14,D16 | SML-D14MWT86A | https://www.digikey.jp/ja/products/detail/rohm-semiconductor/SML-D14MWT86A/9448204
F1,F2 | MF-FSMF020X-2 | https://akizukidenshi.com/catalog/g/g114311/
FB1 | BLM18KG601SN1D | https://www.digikey.jp/ja/products/detail/murata-electronics/BLM18KG601SN1D/1982766
J1 | JS-1200R-06 | https://eleshop.jp/shop/g/g7AB411/
J2 | SM05B-PASS-TBT | https://www.digikey.jp/ja/products/detail/jst-sales-america-inc/SM05B-PASS-TBT/2773428
J3,J4 | SM02B-PASS-TBT | https://www.digikey.jp/ja/products/detail/jst-sales-america-inc/SM02B-PASS-TBT/1788574
J5 | XT60PW-M | https://akizukidenshi.com/catalog/g/g118156/
J6 | XT60PW-F | https://akizukidenshi.com/catalog/g/g118155/
J7 | SM04B-SRSS-TB | https://www.digikey.jp/ja/products/detail/jst-sales-america-inc/SM04B-SRSS-TB/926710
J8 | 5077CR-16-SMC2-BK-TR | https://akizukidenshi.com/catalog/g/g114356/
Q1,Q2 | SQJQ906EL-T1_GE3 | https://www.digikey.jp/ja/products/detail/vishay-siliconix/SQJQ906EL-T1-GE3/6708921
Q3 | BSS138 | https://akizukidenshi.com/catalog/g/g104232/
R1,R10,R22,R23 | ESR03EZPJ431 | https://www.digikey.jp/ja/products/detail/rohm-semiconductor/ESR03EZPJ431/4051257
R2 | ESR03EZPJ121 | https://www.digikey.jp/ja/products/detail/rohm-semiconductor/ESR03EZPJ121/1983454
R3,R31,R32,R35 | ESR03EZPJ101 | https://www.digikey.jp/ja/products/detail/rohm-semiconductor/ESR03EZPJ101/1983452
R4 | ESR03EZPF5900 | https://www.digikey.jp/ja/products/detail/rohm-semiconductor/ESR03EZPF5900/20506305
R5 | ESR03EZPJ301 | https://www.digikey.jp/ja/products/detail/rohm-semiconductor/ESR03EZPJ301/1762729
R6,R7 | ESR03EZPJ331 | https://www.digikey.jp/ja/products/detail/rohm-semiconductor/ESR03EZPJ331/1762730
R8,R9,R16,R17,R26,R27 | ESR03EZPJ820 | https://www.digikey.jp/ja/products/detail/rohm-semiconductor/ESR03EZPJ820/4051294
R11,R18 | ESR03EZPJ152 | https://www.digikey.jp/ja/products/detail/rohm-semiconductor/ESR03EZPJ152/1983456
R12 | RG1608P-133-B-T5 | https://www.digikey.jp/ja/products/detail/susumu/RG1608P-133-B-T5/1240478
R13 | RG1608P-242-B-T5 | https://www.digikey.jp/ja/products/detail/susumu/RG1608P-242-B-T5/1240526
R14 | RG1608P-183-B-T5 | https://www.digikey.jp/ja/products/detail/susumu/RG1608P-183-B-T5/1240502
R15 | RG1608P-302-B-T5 | https://www.digikey.jp/ja/products/detail/susumu/RG1608P-302-B-T5/1240549
R19,R20,R24,R25,R30,R39,R40 | ESR03EZPJ103 | https://www.digikey.jp/ja/products/detail/rohm-semiconductor/ESR03EZPJ103/1762722
R21 | RN73R1JTTD3701B25 | https://www.digikey.jp/ja/products/detail/koa-speer-electronics-inc/RN73R1JTTD3701B25/10016282
R28 | ESR03EZPJ102 | https://www.digikey.jp/ja/products/detail/rohm-semiconductor/ESR03EZPJ102/1762721
R33,R34 | ESR03EZPJ512 | https://www.digikey.jp/ja/products/detail/rohm-semiconductor/ESR03EZPJ512/1762735
R36,R37 | RR0816P-3480-D-53A | https://www.digikey.jp/ja/products/detail/susumu/RR0816P-3480-D-53A/432510
R38 | RMCF0603FT665R | https://www.digikey.jp/ja/products/detail/stackpole-electronics-inc/RMCF0603FT665R/1714186
RV1,RV2 | ST-4ETB103 | https://www.digikey.jp/ja/products/detail/nidec-components-corporation/ST-4ETB103/738213
SW1 | SLW-913535-2A-SMT | https://www.digikey.jp/ja/products/detail/same-sky-formerly-cui-devices/SLW-913535-2A-SMT/21259974
SW2 | RDS-16S-1055-SMT-TR | https://www.digikey.jp/ja/products/detail/same-sky-formerly-cui-devices/RDS-16S-1055-SMT-TR/12424507
SW3 | TVAF06-A020B-R | https://akizukidenshi.com/catalog/g/g114888/
U1 | SMLVN6RGB1W1 | https://www.digikey.jp/ja/products/detail/rohm-semiconductor/SMLVN6RGB1W1/5053781
U2 | NJM7812SDL1 | https://akizukidenshi.com/catalog/g/g110978/
U3 | TLV1117-33CDCYR | https://www.digikey.jp/ja/products/detail/texas-instruments/TLV1117-33CDCYR/1216718
U4 | CZ3A05 | https://www.digikey.jp/ja/products/detail/asahi-kasei-microdevices-akm/CZ3A05/11570592
U5,U6 | IR2302STRPBF | https://akizukidenshi.com/catalog/g/g115656/
U7 | TLP293(BLL-TPL,E(T | https://akizukidenshi.com/catalog/g/g116783/
U8 | STM32F303K8T6 | https://akizukidenshi.com/catalog/g/g110790/
U9 | MCP2562FDT-E/SN | https://www.digikey.jp/ja/products/detail/microchip-technology/MCP2562FDT-E-SN/4860105
U10 | CH340E | https://akizukidenshi.com/catalog/g/g113543/
U11,U12 | TLP2348(V4-TPL,E(T | https://akizukidenshi.com/catalog/g/g118361/
Y1 | XRCGB32M000F1SADR0 | https://www.digikey.jp/ja/products/detail/murata-electronics/XRCGB32M000F1SADR0/21662918

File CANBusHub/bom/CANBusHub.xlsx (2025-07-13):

Reference | Name | URL | Price | Qty | Total
D1 | SML-D12D8WT86 | https://www.digikey.jp/ja/products/detail/rohm-semiconductor/SML-D12D8WT86/1641796 | 28 | 1 | 28
J1,J2,J7,J8 | S04B-PASK-2 | https://www.digikey.jp/ja/products/detail/jst-sales-america-inc/S04B-PASK-2/926755 | 46 | 4 | 184
J3,J4,J5,J6 | FHU-2x42SG | https://akizukidenshi.com/catalog/g/g105780/ | 100 | 4 | 400
J11 | USB4125-GF-A | https://www.digikey.jp/ja/products/detail/gct/USB4125-GF-A/13547388 | 88 | 1 | 88
R1 | ESR03EZPJ431 | https://www.digikey.jp/ja/products/detail/rohm-semiconductor/ESR03EZPJ431/4051257 | 21 | 1 | 21
R2,R3 | ESR03EZPJ512 | https://www.digikey.jp/ja/products/detail/rohm-semiconductor/ESR03EZPJ512/1762735 | 21 | 2 | 42
SW1,SW2,SW3,SW4,SW5,SW6,SW7,SW8 | SLW-913535-2A-SMT | https://www.digikey.jp/ja/products/detail/same-sky-formerly-cui-devices/SLW-913535-2A-SMT/21259974 | 84 | 8 | 672
 |  |  |  | 合計 | 1435 | 円
 |  |  |  | 実質 | 515

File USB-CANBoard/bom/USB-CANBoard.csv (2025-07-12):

Reference | Value | Name | URL | Price | Qty
C1 | 4.7u | GRM188R60J226MEA0D | https://www.digikey.jp/ja/products/detail/murata-electronics/GRM188R60J226MEA0D/4280542 | 30 | 1
C2,C7,C13 | 4.7u | GRM188R60G106ME47D | https://www.digikey.jp/ja/products/detail/murata-electronics/GRM188R60G106ME47D/702562,https://www.digikey.jp/ja/products/detail/murata-electronics/GRM188R60G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 | 19 | 3
C3,C4,C5,C6,C8,C12,C14,C15,C16,C17,C18 | 0.1u | GCJ188R91H124KA01D | https://www.digikey.jp/ja/products/detail/murata-electronics/GCJ188R91H124KA01D/13401917 | 36 | 11
C9 | 1u | GRM188D71H105ME01W | https://www.digikey.jp/ja/products/detail/murata-electronics/GRM188D71H105ME01W/22528412 | 47 | 1
C10,C11 | 12p | GCM1885C2A120JA16D | https://www.digikey.jp/ja/products/detail/murata-electronics/GCM1885C2A120JA16D/2591683 | 15 | 2
D1,D2 | LED | SML-D12D8WT86 | https://www.digikey.jp/ja/products/detail/rohm-semiconductor/SML-D12D8WT86/1641796 | 30 | 2
D3,D4 | D | PMEG3010ER,115 | https://www.digikey.jp/ja/products/detail/nexperia-usa-inc/PMEG3010ER-115/2119868 | 30 | 2
D5,D6,D7,D8,D9 | CAN1_RX,CAN1_TX,CAN2_RX,CAN2_TX,LED | SML-D14MWT86A | https://www.digikey.jp/ja/products/detail/rohm-semiconductor/SML-D14MWT86A/9448204 | 53 | 5
D10,D11 | CAN_R | SMLD12BN1WT86 | https://www.digikey.jp/ja/products/detail/rohm-semiconductor/SMLD12BN1WT86/9826162 | 48 | 2
F1,F2 | Polyfuse | MF-FSMF020X-2 | https://akizukidenshi.com/catalog/g/g114311/ | 20 | 2
FB1 | FerriteBead | BLM18KG601SN1D | https://www.digikey.jp/ja/products/detail/murata-electronics/BLM18KG601SN1D/1982766 | 16 | 1
J1,J2 | DEBUG,USB_FS | 5077CR-16-SMC2-BK-TR | https://akizukidenshi.com/catalog/g/g114356/ | 110 | 2
J3,J4 | CAN1,CAN2 | S04B-PASK-2 | https://www.digikey.jp/ja/products/detail/jst-sales-america-inc/S04B-PASK-2/926755 | 46 | 2
J5 | SWD | SM04B-SRSS-TB | https://www.digikey.jp/ja/products/detail/jst-sales-america-inc/SM04B-SRSS-TB/926710 | 81 | 1
R1,R2,R15,R17 | 420,430 | ESR03EZPJ431 | https://www.digikey.jp/ja/products/detail/rohm-semiconductor/ESR03EZPJ431/4051257 | 22 | 4
R3,R4 | 10k | ESR03EZPJ103 | https://www.digikey.jp/ja/products/detail/rohm-semiconductor/ESR03EZPJ103/1762722 | 22 | 2
R5,R6,R7,R8 | 5.1k | ESR03EZPJ512 | https://www.digikey.jp/ja/products/detail/rohm-semiconductor/ESR03EZPJ512/1762735 | 22 | 4
R9,R10,R11,R12,R13,R18 | 100,96 | ESR03EZPJ101 | https://www.digikey.jp/ja/products/detail/rohm-semiconductor/ESR03EZPJ101/1983452 | 22 | 6
R14,R16 | 120 | ESR03EZPJ121 | https://www.digikey.jp/ja/products/detail/rohm-semiconductor/ESR03EZPJ121/1983454 | 22 | 2
R19 | 600 | ESR03EZPF5900 | https://www.digikey.jp/ja/products/detail/rohm-semiconductor/ESR03EZPF5900/20506305 | 22 | 1
R20 | 300 | ESR03EZPJ301 | https://www.digikey.jp/ja/products/detail/rohm-semiconductor/ESR03EZPJ301/1762729 | 22 | 1
SW1 | RESET | TVAF06-A020B-R | https://akizukidenshi.com/catalog/g/g114888/ | 22 | 1
SW2,SW3 | CAN_R | SLW-913535-2A-SMT | https://www.digikey.jp/ja/products/detail/same-sky-formerly-cui-devices/SLW-913535-2A-SMT/21259974 | 87 | 2
U2 | TLV1117-33 | TLV1117-33CDCYR | https://www.digikey.jp/ja/products/detail/texas-instruments/TLV1117-33CDCYR/1216718 | 63 | 1
U3 | CH340E | CH340E | https://akizukidenshi.com/catalog/g/g113543/ | 90 | 1
U4,U5 | ISO1044BD | ISO1044BD | https://www.digikey.jp/ja/products/detail/texas-instruments/ISO1044BD/13237251 | 540 | 2
U6 | LED_GRB | SMLVN6RGB1W1 | https://www.digikey.jp/ja/products/detail/rohm-semiconductor/SMLVN6RGB1W1/5053781 | 244 | 1
Y1 | 26MHz | XRCGB26M000F1SADR0 | https://www.digikey.jp/ja/products/detail/murata-electronics/XRCGB26M000F1SADR0/21662900 | 50 | 1

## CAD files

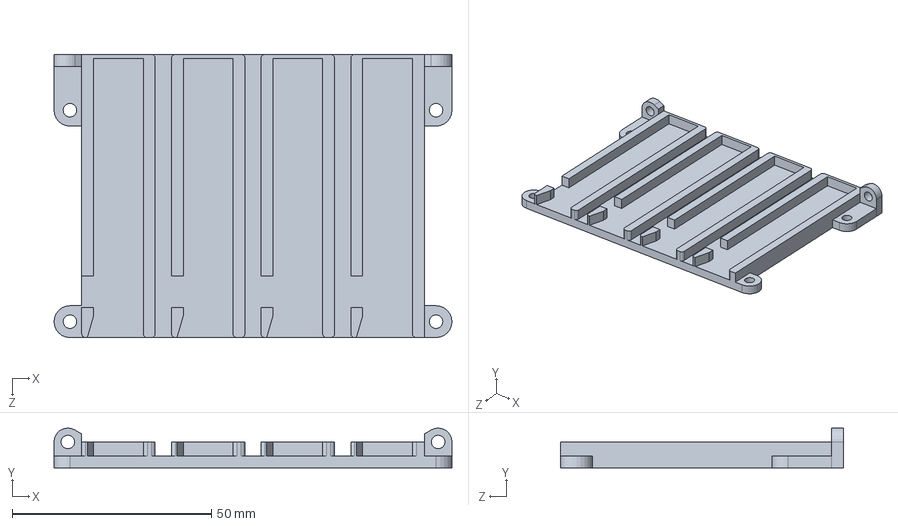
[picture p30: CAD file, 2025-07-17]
3D/BoardFixer/parts/base.SLDPRT
99.8 x 9.97 x 71.1 mm

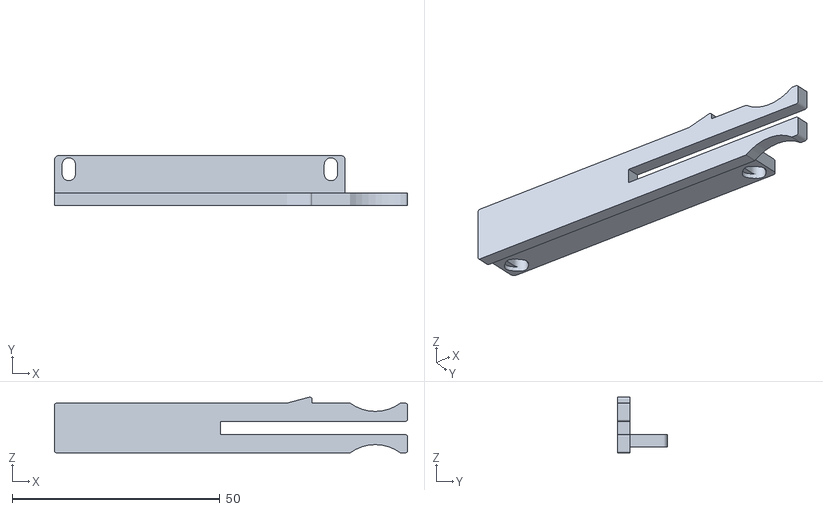
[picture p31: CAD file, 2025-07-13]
3D/BoardFixer/parts/stl/slide.STL
85.0 x 12.0 x 13.4

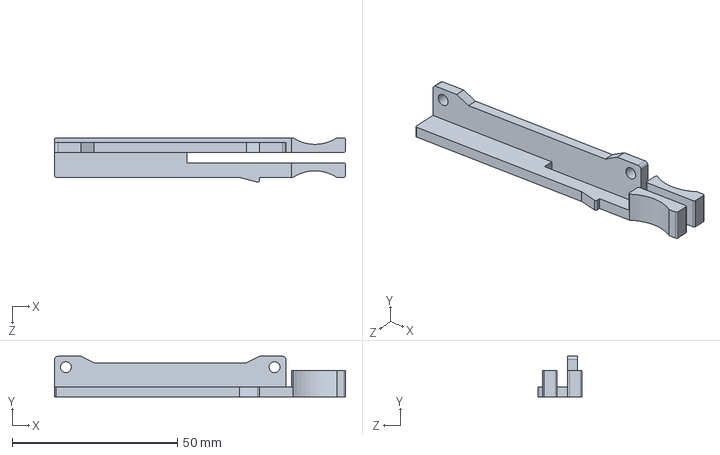
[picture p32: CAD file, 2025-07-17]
3D/BoardFixer/parts/slider.SLDPRT
88.0 x 12.2 x 13.4 mm

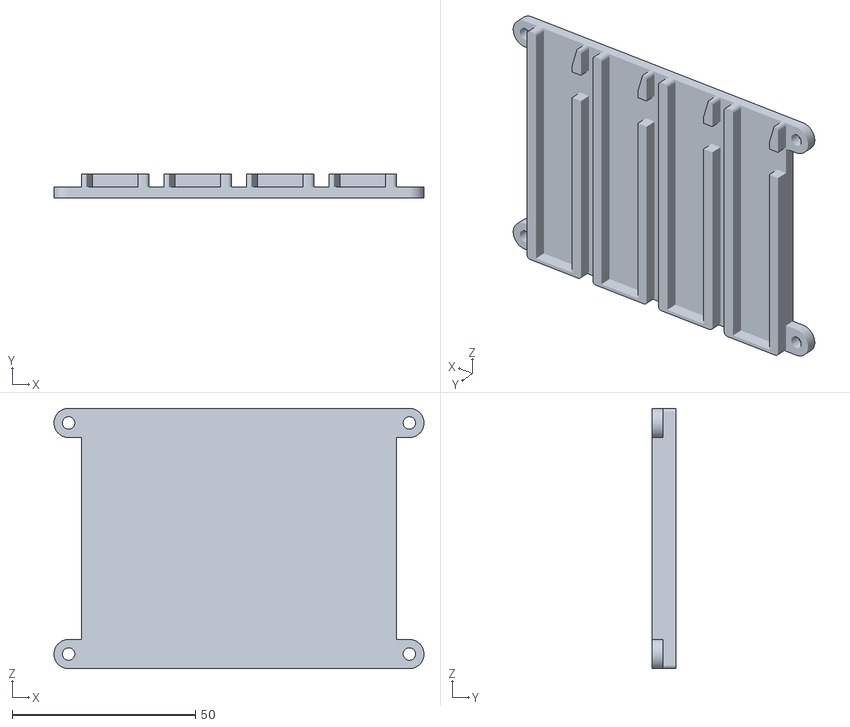
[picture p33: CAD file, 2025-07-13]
3D/BoardFixer/parts/stl/base_x4.STL
100.9 x 6.50 x 71.1

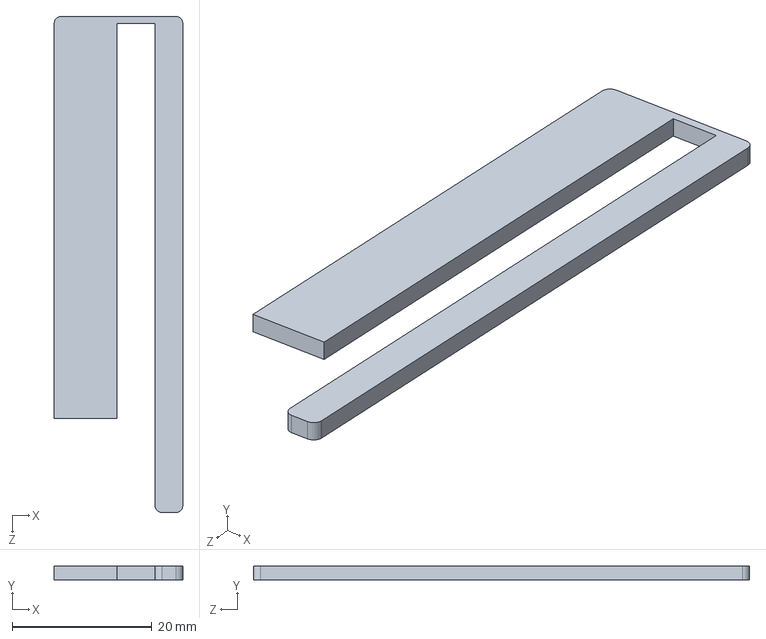
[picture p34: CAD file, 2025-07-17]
3D/BoardFixer/parts/base_cap.SLDPRT
18.4 x 2.00 x 71.0 mm

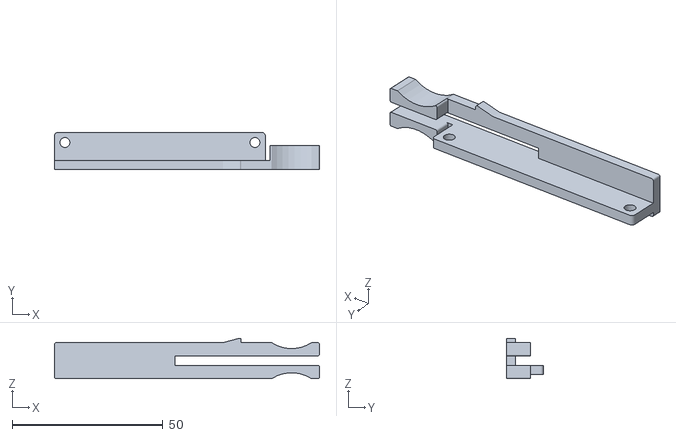
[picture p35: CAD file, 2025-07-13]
3D/BoardFixer/parts/stl/slide2.STL
88.0 x 12.2 x 13.4

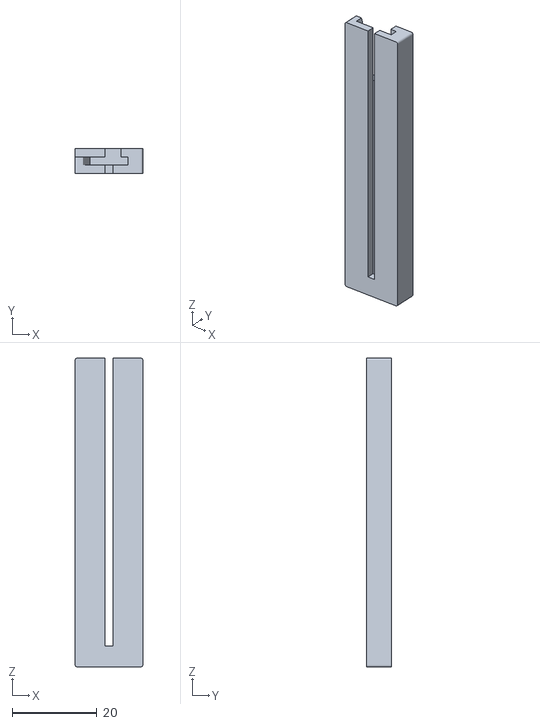
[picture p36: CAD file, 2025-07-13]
3D/BoardFixer/parts/stl/base2.STL
16.0 x 6.00 x 73.1

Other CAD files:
3D/BoardFixer/parts/stl/base1.STL
3D/BoardFixer/parts/stl/base.STL
3D/BoardFixer/parts/stl/base_cap.3mf
3D/BoardFixer/parts/stl/base_cap.STL

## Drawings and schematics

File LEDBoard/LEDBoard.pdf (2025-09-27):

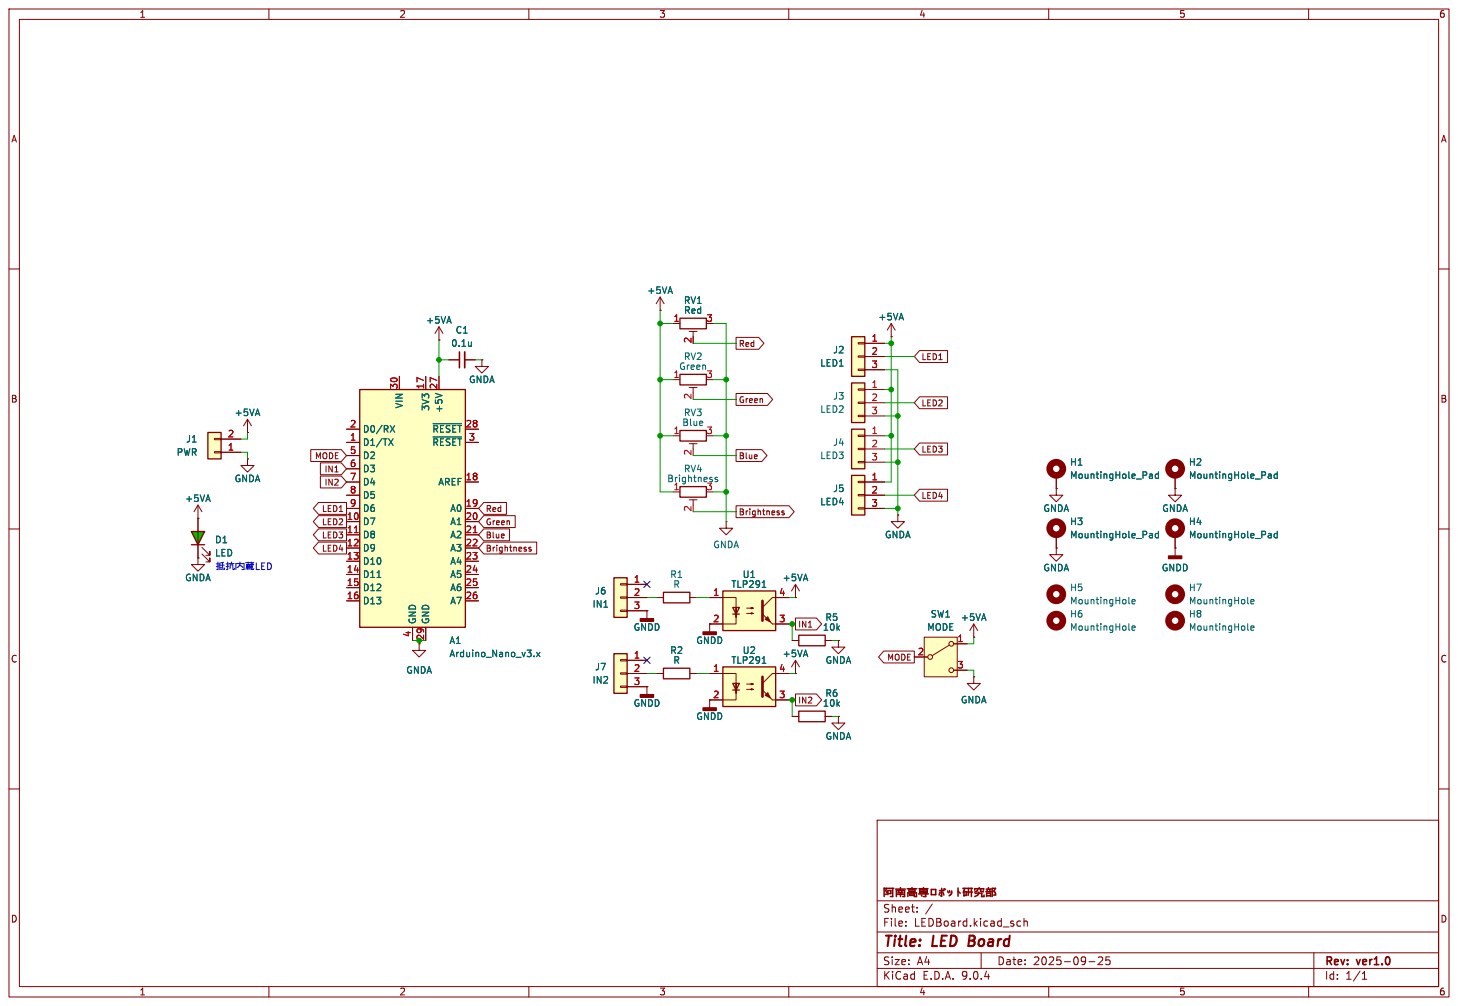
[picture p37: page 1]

File: LEDBoard.kicad_sch Sheet: / þÿ–?SWšØ\-

Id: 1/1 Title: LED Board

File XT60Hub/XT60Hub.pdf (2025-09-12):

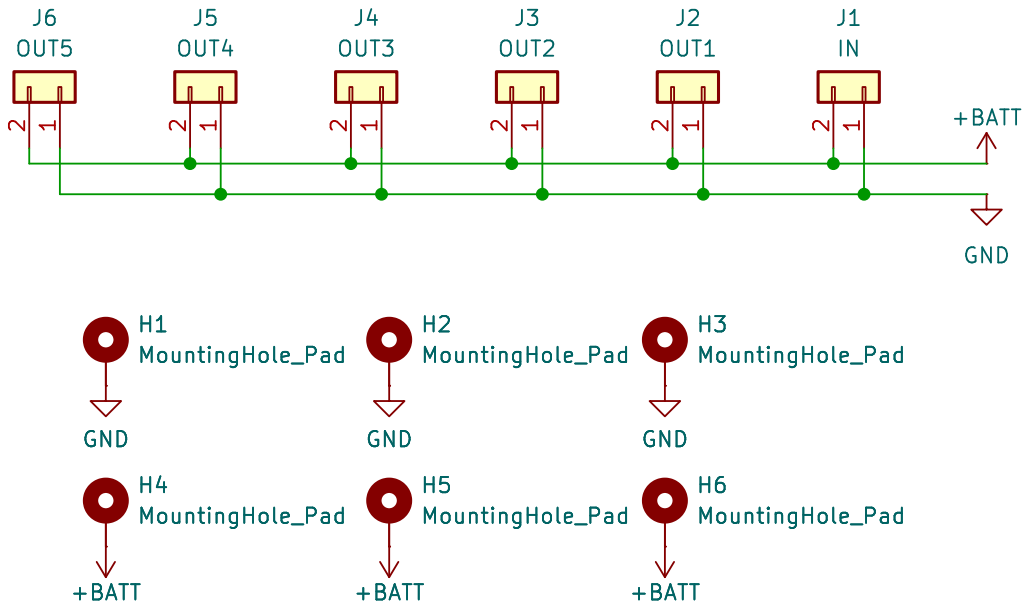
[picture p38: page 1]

File: XT60Hub.kicad_sch Sheet: / þÿ–?SWšØ\-

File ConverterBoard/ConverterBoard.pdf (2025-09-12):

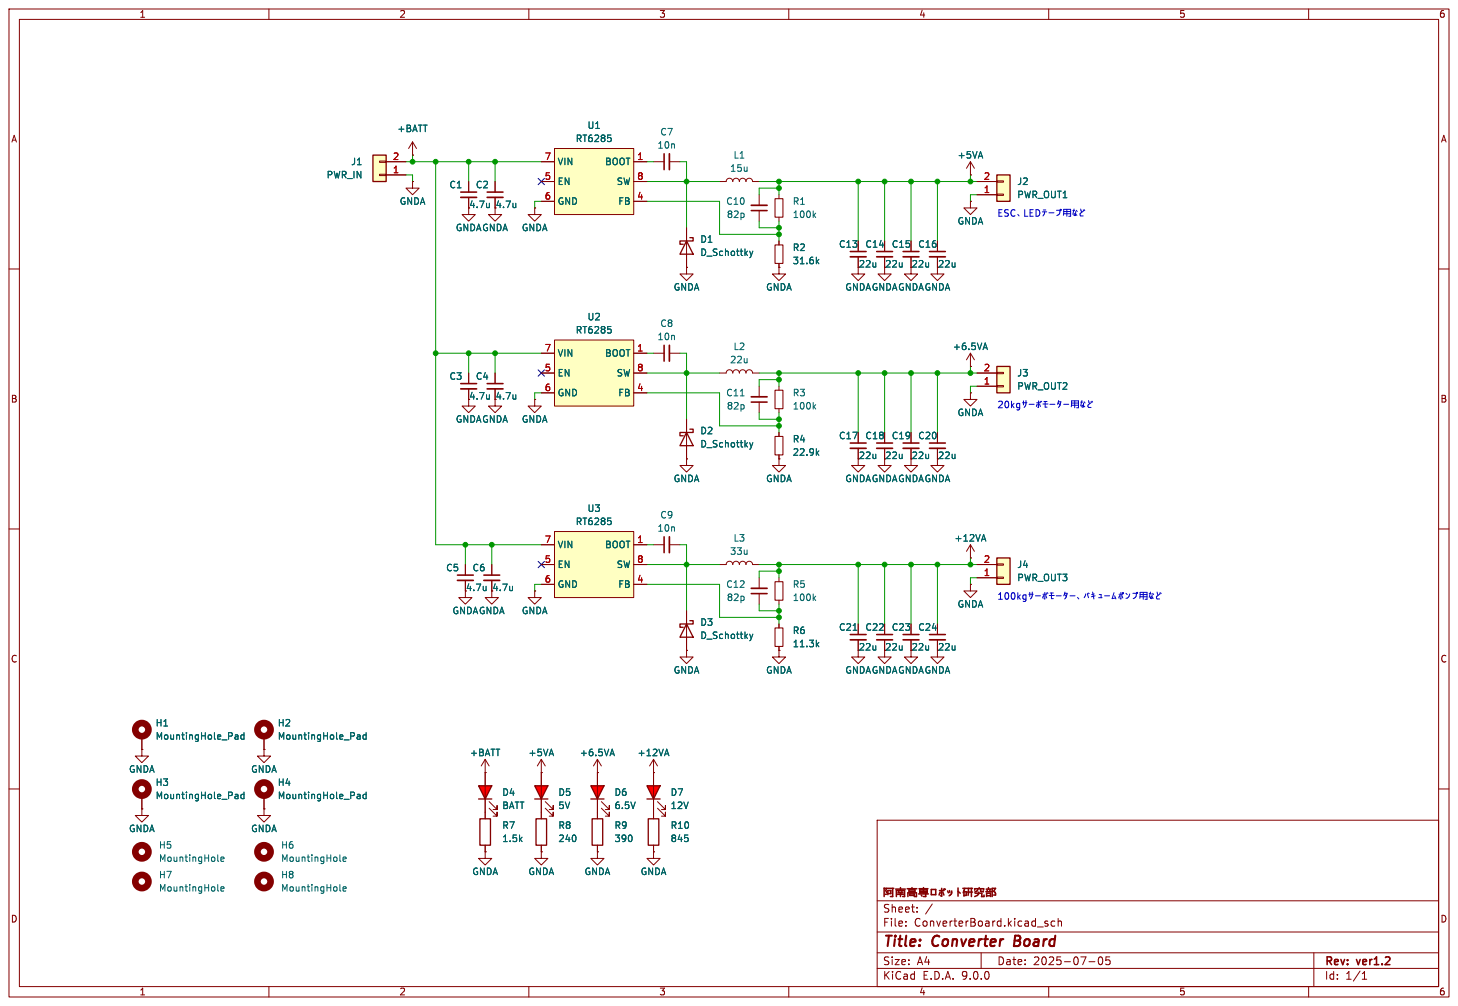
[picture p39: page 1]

File: ConverterBoard.kicad_sch Sheet: / þÿ–?SWšØ\-

Id: 1/1 Title: Converter Board

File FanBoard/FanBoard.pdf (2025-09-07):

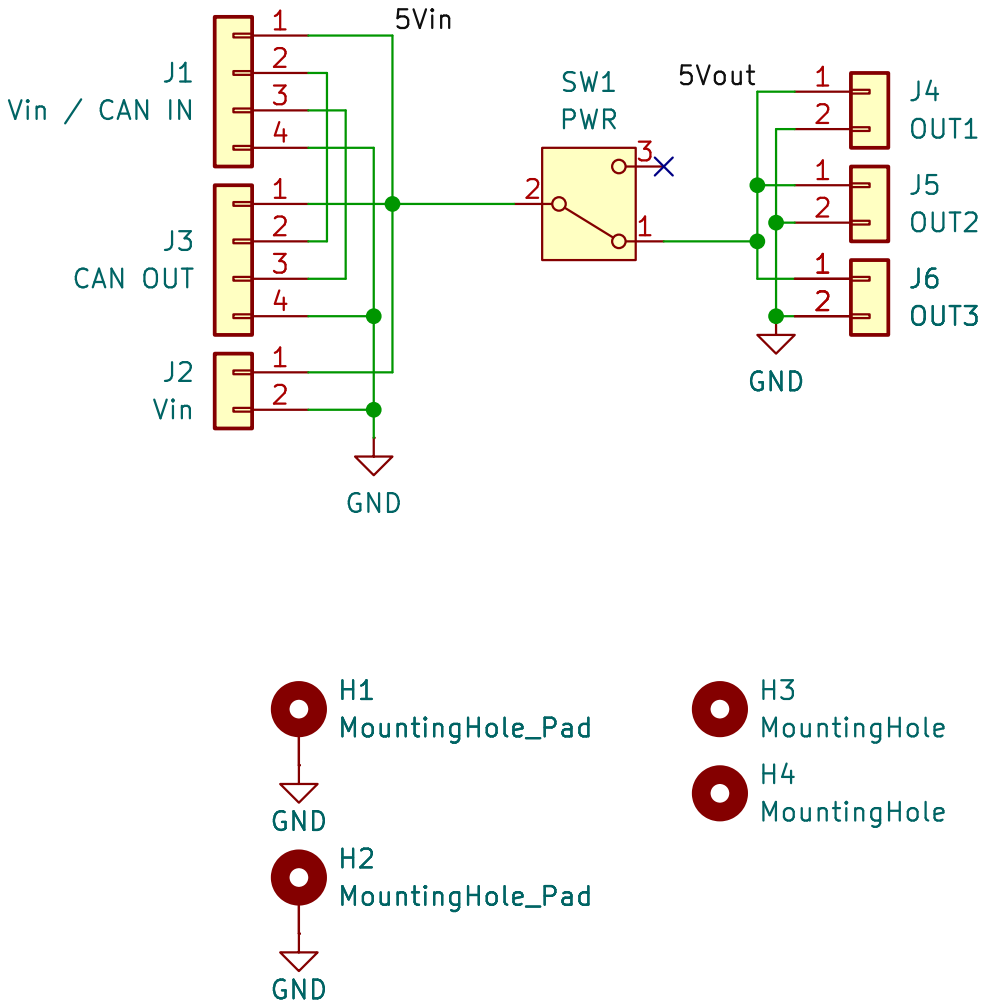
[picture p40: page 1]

File: FanBoard.kicad_sch Sheet: / þÿ–?SWšØ\-

Id: 1/1 Title: Fan Board

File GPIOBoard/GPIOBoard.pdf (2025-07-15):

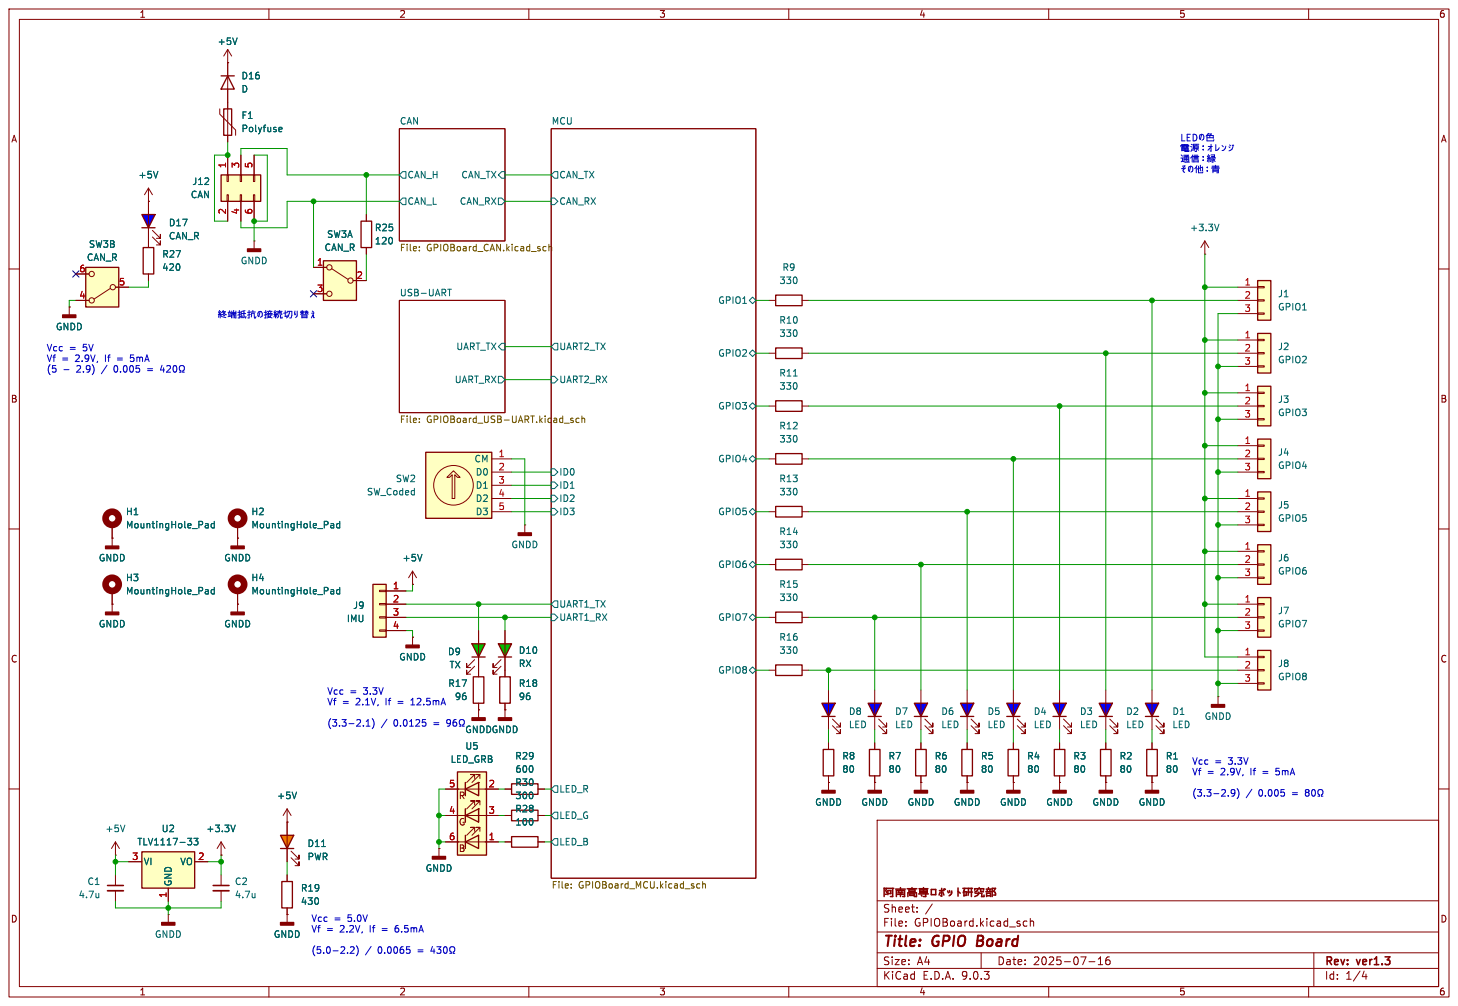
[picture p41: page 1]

File: GPIOBoard.kicad_sch Sheet: / þÿ–?SWšØ\-

Id: 1/4 Title: GPIO Board

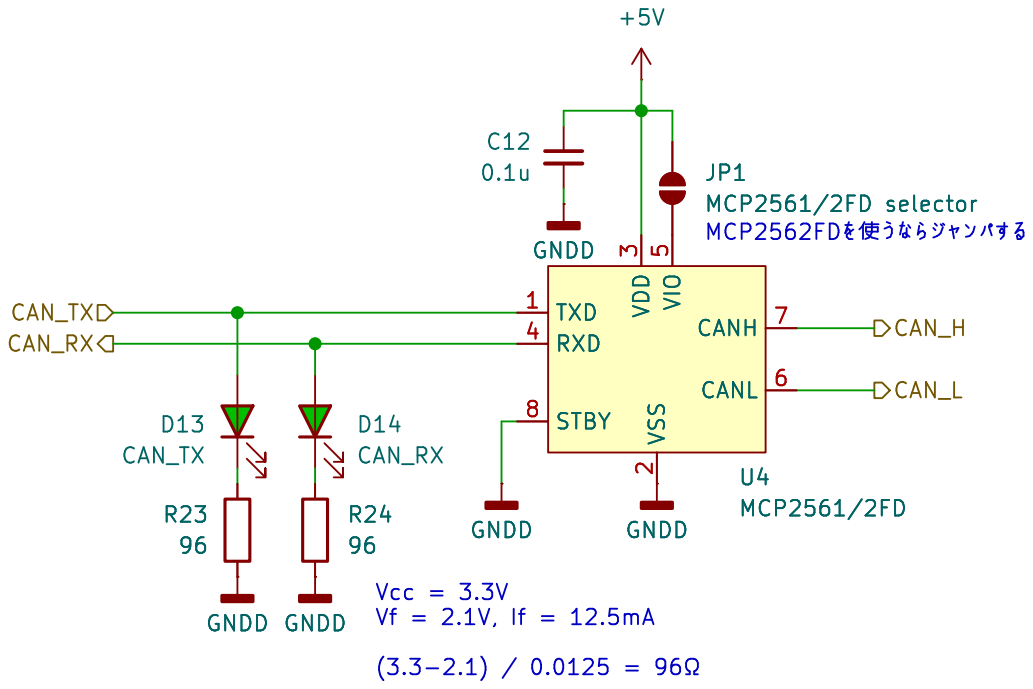
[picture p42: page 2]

File: GPIOBoard_CAN.kicad_sch Sheet: /CAN/ þÿ–?SWšØ\-

Id: 4/4 Title: GPIO Board / CAN

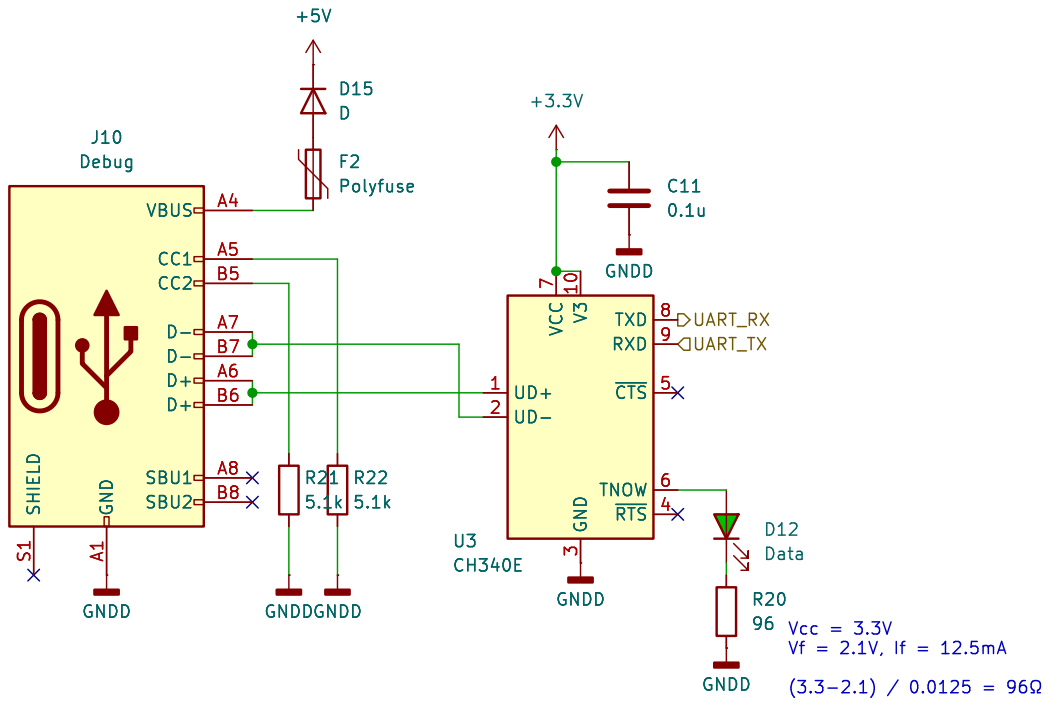
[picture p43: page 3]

3 TXD 8 RXD 9 ~{CTS}5 TNOW 6 ~{RTS}4 U3 CH340E GNDD SHIELD S1 GND A1 VBUS A4 CC1 A5 CC2 B5 D- A7 D- B7 D+ A6 D+ B6 SBU1 A8 SBU2 B8

3 TXD 8 RXD 9 ~{CTS}5 TNOW 6 ~{RTS}4 GNDD

File: GPIOBoard_USB-UART.kicad_sch Sheet: /USB-UART/ þÿ–?SWšØ\-

Id: 3/4 Title: GPIO Board / USB-UART

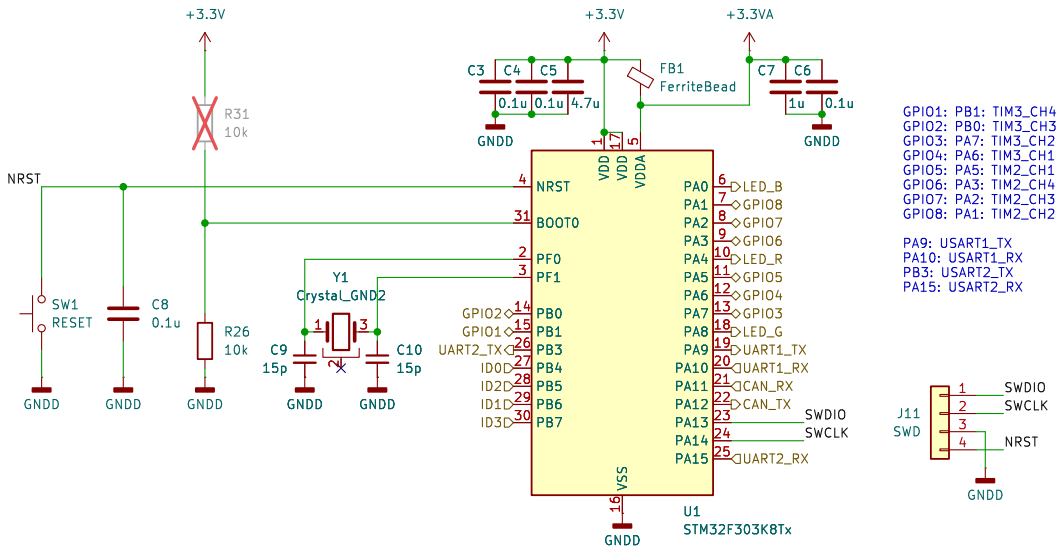
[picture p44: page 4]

File: GPIOBoard_MCU.kicad_sch Sheet: /MCU/ þÿ–?SWšØ\-

Id: 2/4 Title: GPIO Board / MCU

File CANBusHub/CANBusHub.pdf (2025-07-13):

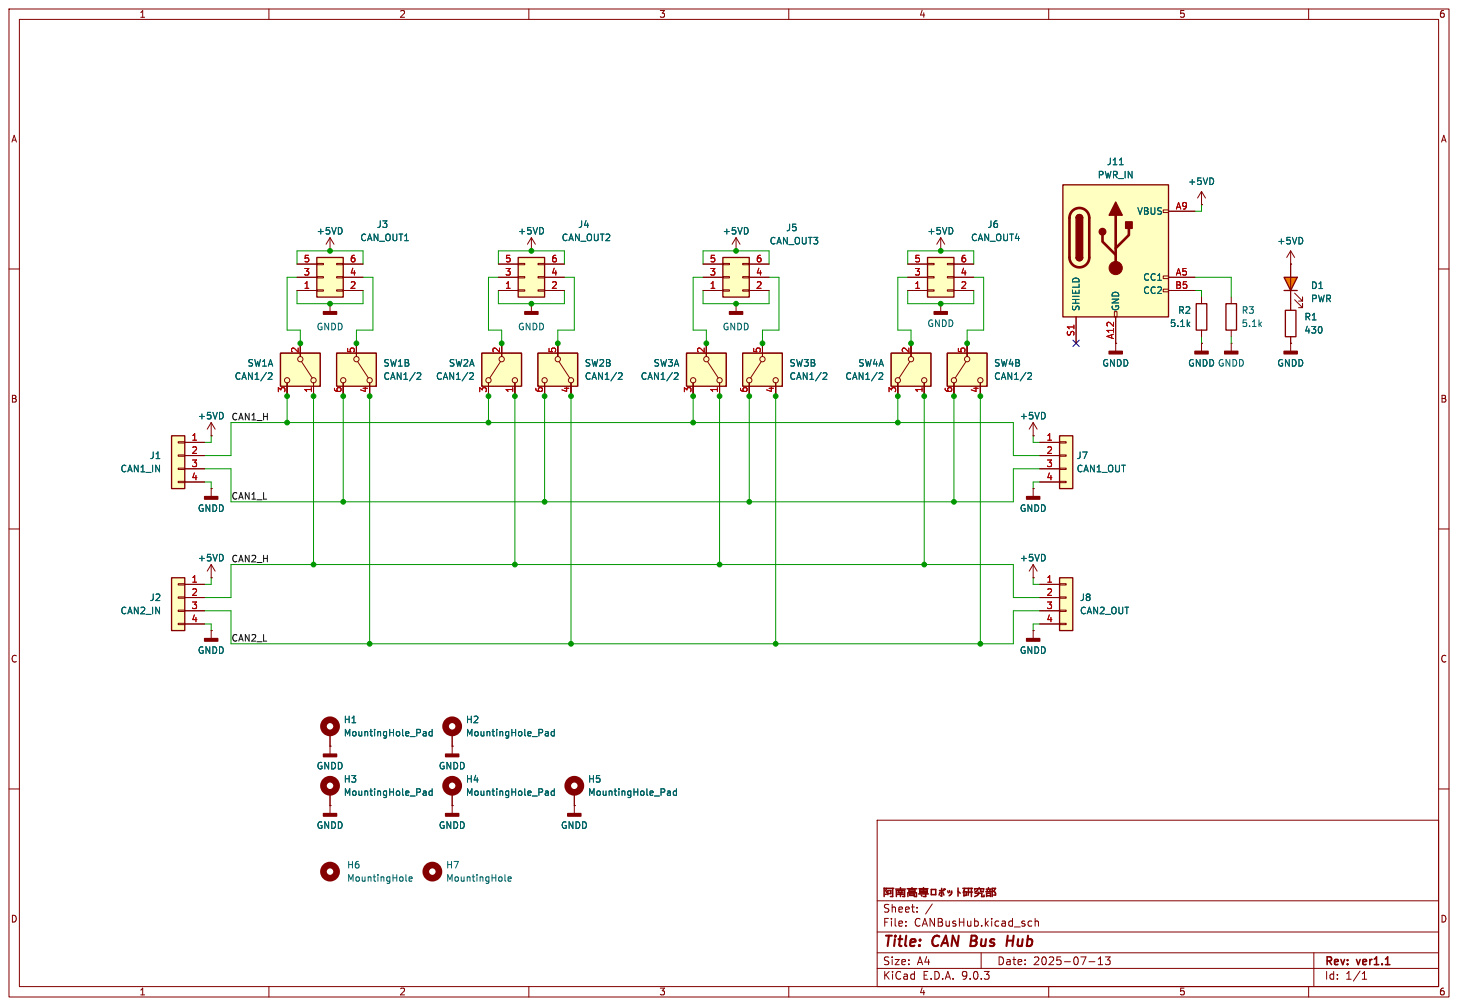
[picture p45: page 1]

File: CANBusHub.kicad_sch Sheet: / þÿ–?SWšØ\-

Id: 1/1 Title: CAN Bus Hub

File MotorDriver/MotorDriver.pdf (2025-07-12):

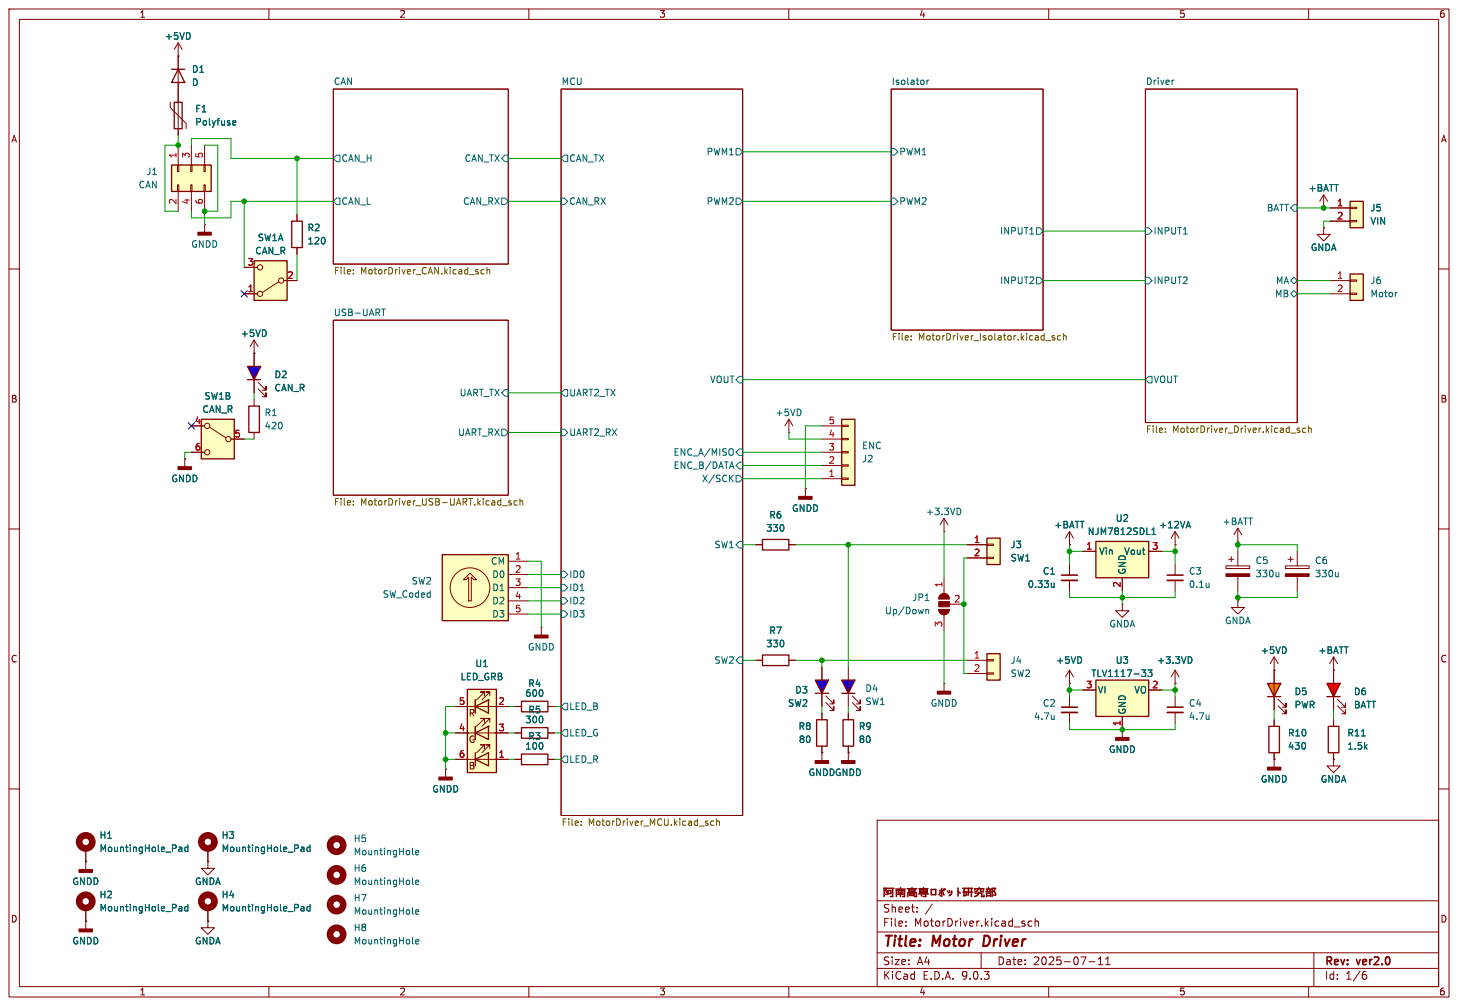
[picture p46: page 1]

Isolator File: MotorDriver_Isolator.kicad_sch UART_RX UART_TX USB-UART

1 VO 2 U3 TLV1117-33 CM 1 D0 2 D1 3 D2 4 D3 5 SW2 SW_Coded GNDA H6 MountingHole H8 MountingHole H7 MountingHole GNDD

Id: 1/6 Title: Motor Driver File: MotorDriver.kicad_sch Sheet: / þÿ–?SWšØ\-

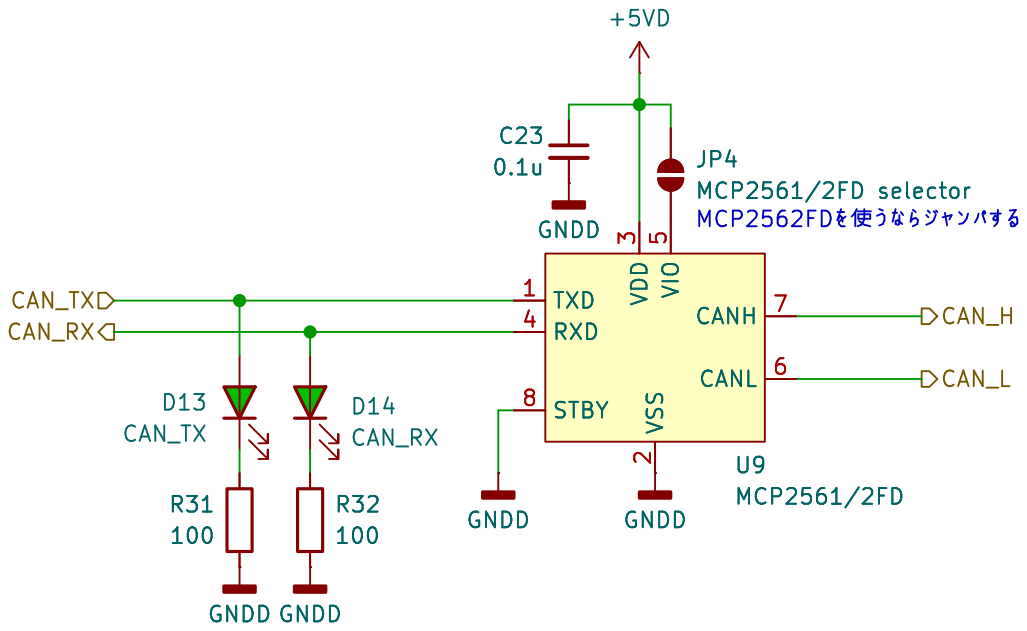
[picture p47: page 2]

File: MotorDriver_CAN.kicad_sch Sheet: /CAN/ þÿ–?SWšØ\-

Id: 4/6 Title: MotorDriver / MCU

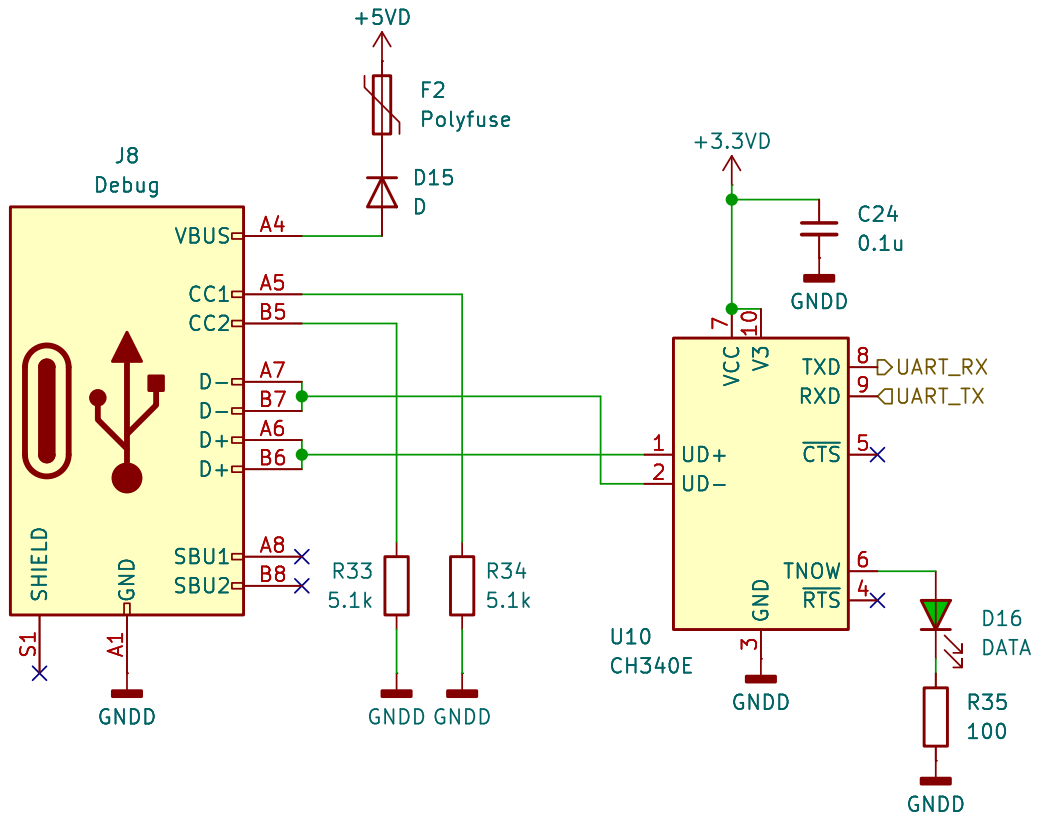
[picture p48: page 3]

3 TXD 8 RXD 9 ~{CTS}5 TNOW 6 ~{RTS}4 U10 CH340E GNDD

3 TXD 8 RXD 9 ~{CTS}5 TNOW 6 ~{RTS}4 GNDD R35

File: MotorDriver_USB-UART.kicad_sch Sheet: /USB-UART/ þÿ–?SWšØ\-

Id: 5/6 Title: MotorDriver / USB-UART


File: MotorDriver_MCU.kicad_sch Sheet: /MCU/ þÿ–?SWšØ\-

Id: 3/6 Title: MotorDriver / MCU


Id: 6/6 Title: MotorDriver / Isolator File: MotorDriver_Isolator.kicad_sch Sheet: /Isolator/ þÿ–?SWšØ\-


Id: 2/6 Title: MotorDriver / Driver File: MotorDriver_Driver.kicad_sch Sheet: /Driver/

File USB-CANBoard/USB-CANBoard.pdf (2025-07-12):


File: USB-CANBoard.kicad_sch Sheet: / þÿ–?SWšØ\-

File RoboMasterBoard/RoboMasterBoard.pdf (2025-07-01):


File: RoboMasterBoard.kicad_sch Sheet: / þÿ–?SWšØ\-

Id: 1/5 Title: RoboMaster Board


1 VDD 19 VDD 32 VSS 18 VDD 48 VSSA 12 VDD 64 VDDA 13 PA0 14 PA1 15 PA2 16 PA3 17 PA4 20 PA5 21 PA6 22 PA7 23 PA8 41 PA9 42 PA10 43 PA11 44 PA12 45 PA13 46 PA14 49 PA15 50 PB0 26 PB1 27 PB2 28 PB3 55 PB4 56 PB5 57 PB6 58 PB7 59 PB8 61 PB9 62 PB10 29 PB12 33 PB13 34 PB14 35 PB15 36 U2STM32F446RETx GNDD

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

File: RoboMasterBoard_MCU.kicad_sch Sheet: /MCU/ þÿ–?SWšØ\-

Id: 2/5 Title: RoboMaster Board / MCU


File: RoboMasterBoard_CAN1.kicad_sch Sheet: /CAN1/ þÿ–?SWšØ\-

Id: 3/5 Title: RoboMaster Board / CAN1


5 CANH 7 CANL 6 GNDD GNDD GNDD GNDD

5 CANH 7 CANL 6 U4 MCP2561/2FD GNDD GNDD GNDD

File: RoboMasterBoard_CAN2.kicad_sch Sheet: /CAN2/ þÿ–?SWšØ\-

Id: 4/5 Title: RoboMaster Board / CAN2


File: RoboMasterBoard_USB.kicad_sch Sheet: /USB/ þÿ–?SWšØ\-

Id: 5/5 Title: RoboMaster Board / USB

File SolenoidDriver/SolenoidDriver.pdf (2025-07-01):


Id: 1/6 Title: Solenoid Driver File: SolenoidDriver.kicad_sch Sheet: / þÿ–?SWšØ\-


File: SolenoidDriver_MCU.kicad_sch Sheet: /MCU/ þÿ–?SWšØ\-

Id: 2/6 Title: Solenoid Driver / MCU


5 CANH 7 CANL 6 U3 MCP2561/2FD GNDD GNDD

File: SolenoidDriver_CAN.kicad_sch Sheet: /CAN/ þÿ–?SWšØ\-

Id: 3/6 Title: Solenoid Driver / CAN


3 TXD 8 RXD 9 ~{CTS}5 TNOW 6 ~{RTS}4 U4 CH340E GNDD GNDD

3 TXD 8 RXD 9 ~{CTS}5 TNOW 6 ~{RTS}4 GNDD GNDD

File: SolenoidDriver_USB-UART.kicad_sch Sheet: /USB-UART/ þÿ–?SWšØ\-

Id: 4/6 Title: Solenoid Driver / USB-UART


Id: 5/6 Title: Solenoid Driver / Isolator File: SolenoidDriver_Isolator.kicad_sch Sheet: /Isolator/ þÿ–?SWšØ\-


File: SolenoidDriver_MOSFET.kicad_sch Sheet: /MOSFET/ þÿ–?SWšØ\-

Id: 6/6 Title: Solenoid Driver / MOSFET

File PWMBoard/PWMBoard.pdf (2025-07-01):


File: PWMBoard.kicad_sch Sheet: / þÿ–?SWšØ\-

Id: 1/5 Title: PWM Board


File: PWMBoard_MCU.kicad_sch Sheet: /MCU/ þÿ–?SWšØ\-

Id: 2/5 Title: PWM Board / MCU


5 CANH 7 CANL 6 GNDD GNDD GNDD

5 CANH 7 CANL 6 U3 MCP2561/2FD GNDD GNDD

File: PWMBoard_CAN.kicad_sch Sheet: /CAN/ þÿ–?SWšØ\-

Id: 3/5 Title: PWM Board / CAN


3 TXD 8 RXD 9 ~{CTS}5 TNOW 6 ~{RTS}4 U6 CH340E D5 D
0.1u GNDD GNDD

3 TXD 8 RXD 9 ~{CTS}5 TNOW 6 ~{RTS}4 D5 D

File: PWMBoard_USB-UART.kicad_sch Sheet: /USB-UART/ þÿ–?SWšØ\-

Id: 4/5 Title: PWM Board / USB-UART


9 OUTA 14 OUTB 13 OUTC 12 OUTD 11 EN2 10 GNDD

9 OUTA 14 OUTB 13 OUTC 12 OUTD 11 EN2 10U4

9 OUTA 14 OUTB 13 OUTC 12 OUTD 11 EN2 10U5

Id: 5/5 Title: PWM Board / Isolator File: PWMBoard_Isolator.kicad_sch Sheet: /Isolator/ þÿ–?SWšØ\-


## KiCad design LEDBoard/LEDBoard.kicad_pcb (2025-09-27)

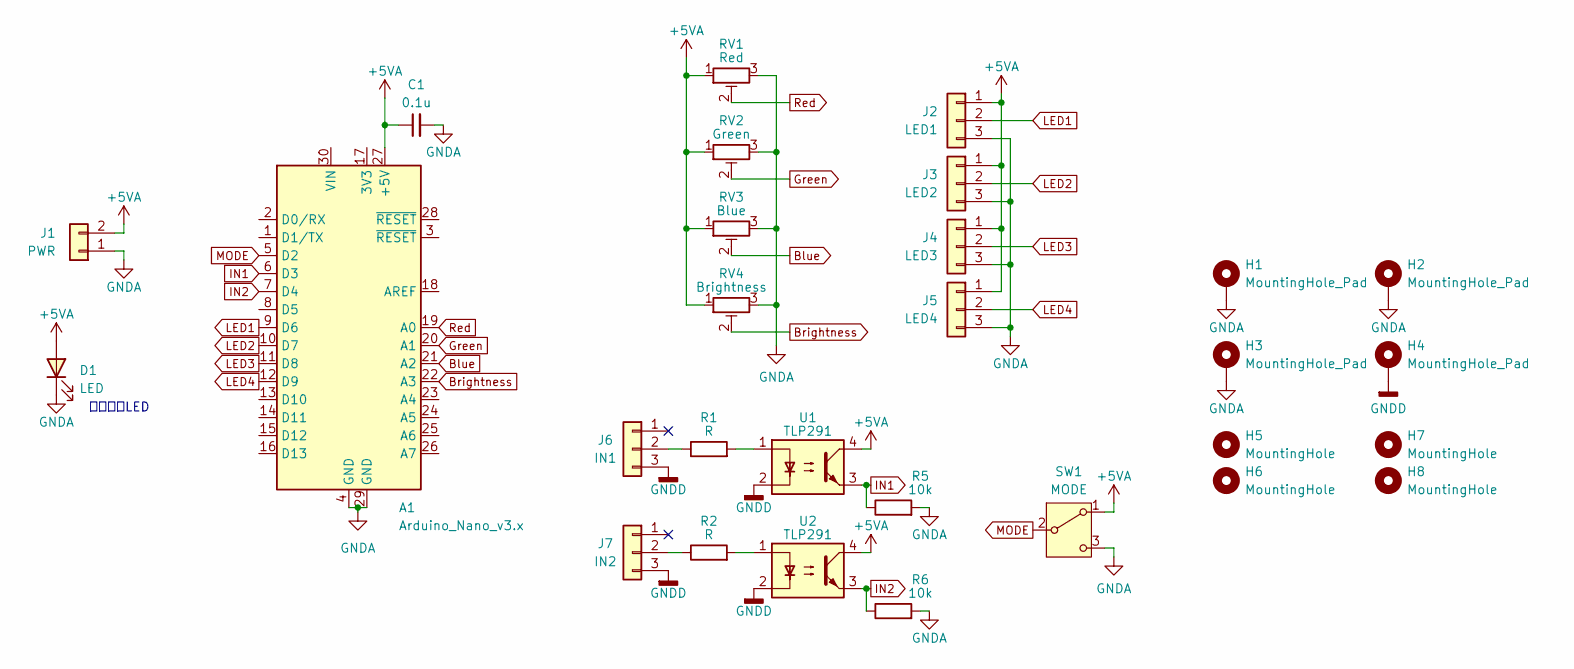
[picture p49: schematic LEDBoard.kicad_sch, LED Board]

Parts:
A1: Arduino_Nano_v3.x; Arduino_Nano
C1: 0.1u; C_0603_1608Metric
D1: LED; LED_D5.0mm
H1, H2, H3, H4: MountingHole_Pad; MountingHole_3.2mm_M3_Pad
H5: MountingHole; Title
H6: MountingHole; Info_L
H7: MountingHole; Aho_old_S
H8: MountingHole; Aho_new_S
J1: PWR; AMASS_XT30U-M_1x02_P5.0mm_Vertical
J2: LED1; PAコネクタ(3ピントップ型)
J3: LED2; PAコネクタ(3ピントップ型)
J4: LED3; PAコネクタ(3ピントップ型)
J5: LED4; PAコネクタ(3ピントップ型)
J6: IN1; PAコネクタ(3ピントップ型)
J7: IN2; PAコネクタ(3ピントップ型)
R1, R2: R; R_0603_1608Metric
R5, R6: 10k; R_0603_1608Metric
RV1: Red; TSR-3386K
RV2: Green; TSR-3386K
RV3: Blue; TSR-3386K
RV4: Brightness; TSR-3386K
SW1: MODE; SS-12D00G3
U1, U2: TLP291; SOIC-4_4.55x2.6mm_P1.27mm

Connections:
+5VA: A1.27 (+5V), C1.1, D1.2 (A), J1.2, J2.1, J3.1, J4.1, J5.1, RV1.1, RV2.1, RV3.1, RV4.1, SW1.1 (A), U1.4, U2.4
Blue: A1.21 (A2), RV3.2
Brightness: A1.22 (A3), RV4.2
GNDA: A1.4 (GND), A1.29 (GND), C1.2, D1.1 (K), H1.1, H2.1, H3.1, J1.1, J2.3, J3.3, J4.3, J5.3, R5.2, R6.2, RV1.3, RV2.3, RV3.3, RV4.3, SW1.3 (C)
GNDD: H4.1, J6.3, J7.3, U1.2, U2.2
Green: A1.20 (A1), RV2.2
IN1: A1.6 (D3), R5.1, U1.3
IN2: A1.7 (D4), R6.1, U2.3
LED1: A1.9 (D6), J2.2
LED2: A1.10 (D7), J3.2
LED3: A1.11 (D8), J4.2
LED4: A1.12 (D9), J5.2
MODE: A1.5 (D2), SW1.2 (B)
unnamed: J6.2, R1.1
unnamed: J7.2, R2.1
unnamed: R1.2, U1.1
unnamed: R2.2, U2.1
Red: A1.19 (A0), RV1.2

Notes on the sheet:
抵抗内蔵LED

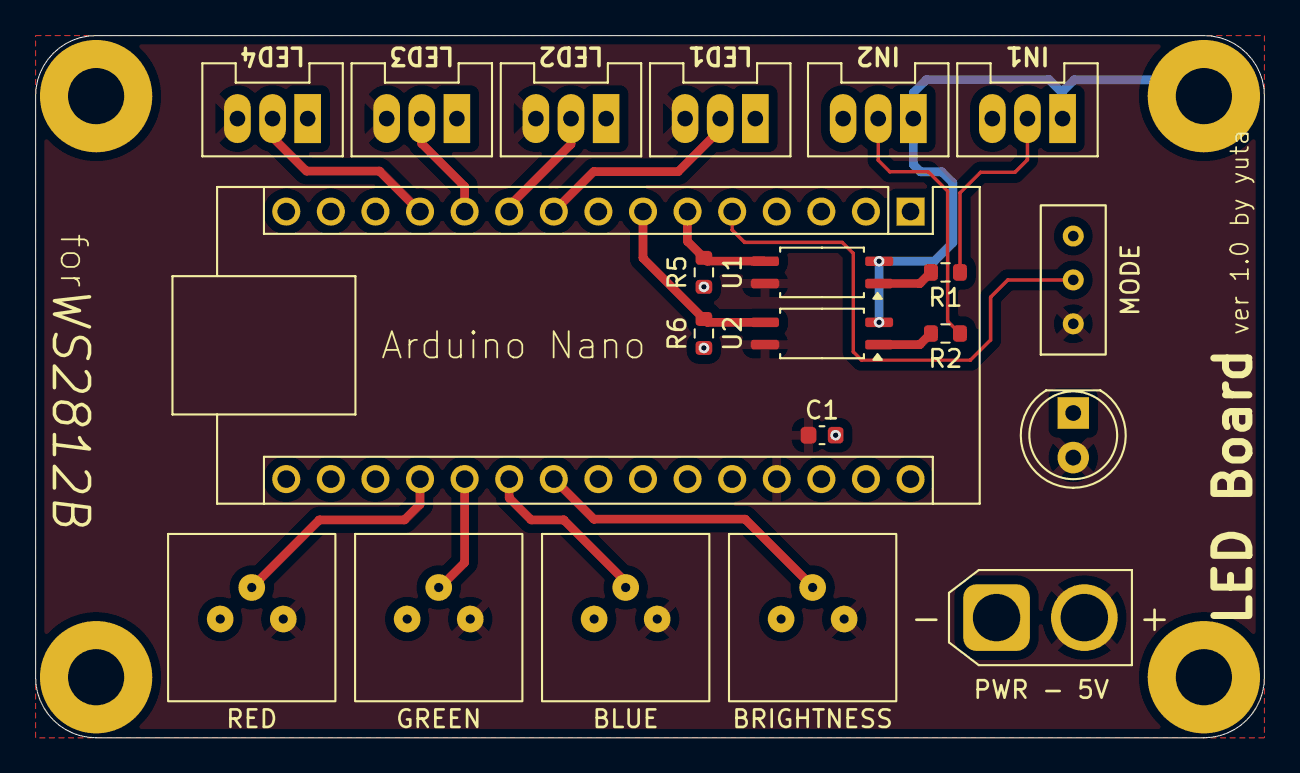
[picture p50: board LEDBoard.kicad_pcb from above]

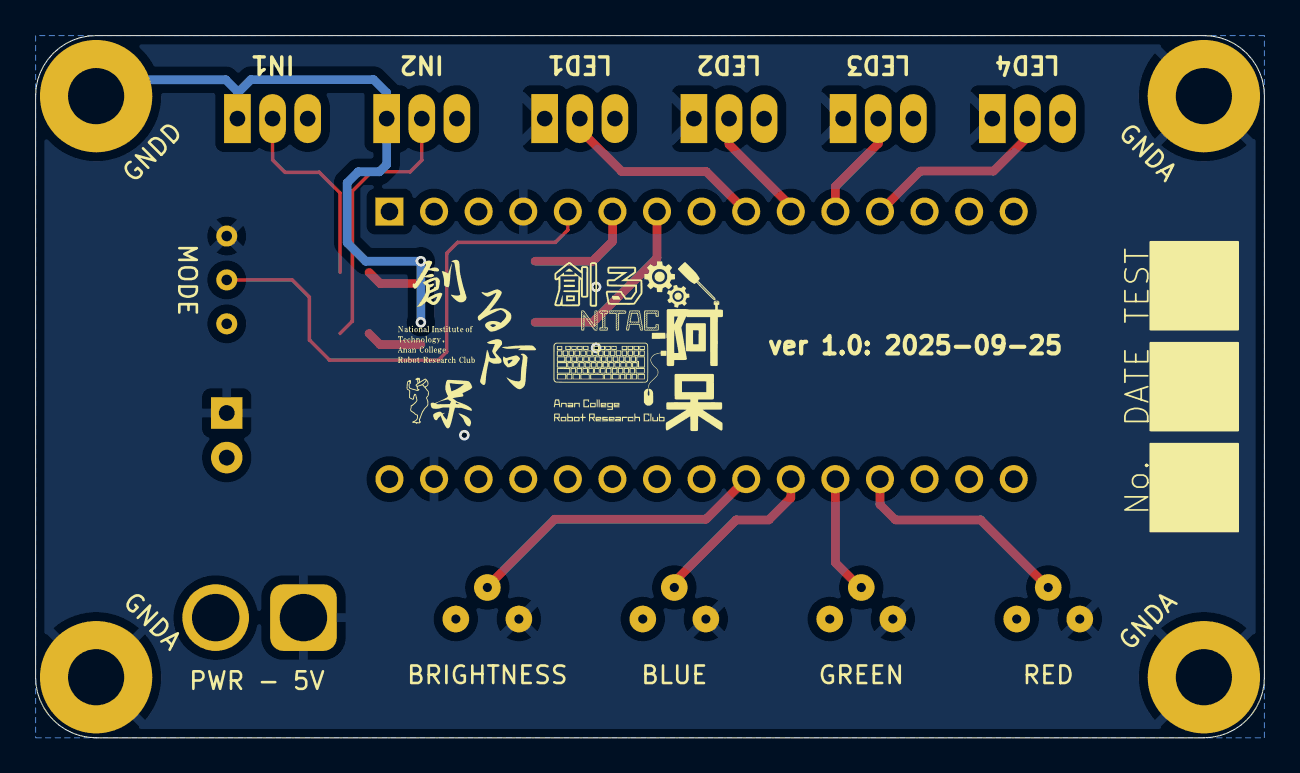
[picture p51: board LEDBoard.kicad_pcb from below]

Board: 2 copper layers, 70.0 x 40.0 mm, 29 parts (3 on the bottom side), 18 nets.

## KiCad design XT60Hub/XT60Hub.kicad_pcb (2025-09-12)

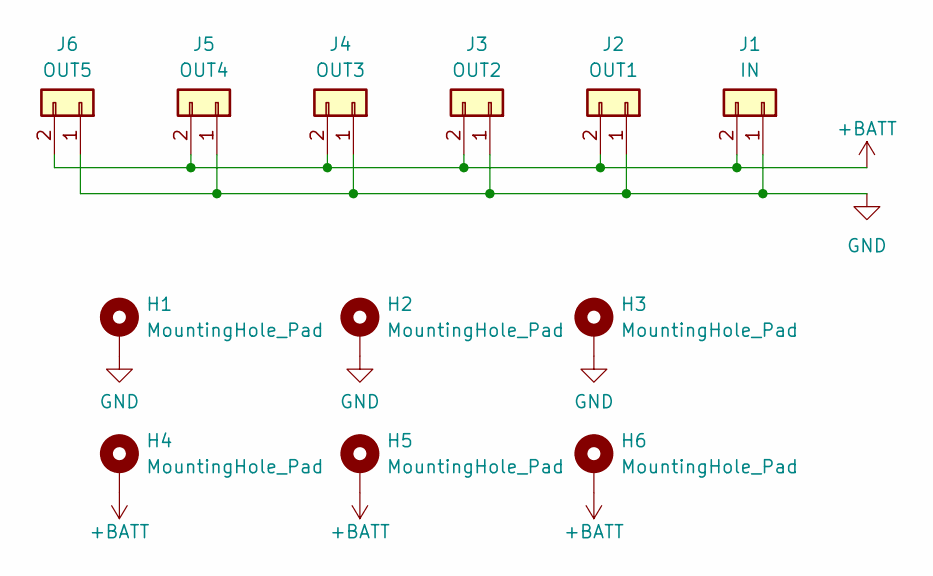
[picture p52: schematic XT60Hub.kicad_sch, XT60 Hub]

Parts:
H1, H2, H3, H4, H5, H6: MountingHole_Pad; MountingHole_3.2mm_M3_Pad
J1: IN; AMASS_XT60-M_1x02_P7.20mm_Vertical
J2: OUT1; AMASS_XT60-F_1x02_P7.20mm_Vertical
J3: OUT2; AMASS_XT60-F_1x02_P7.20mm_Vertical
J4: OUT3; AMASS_XT60-F_1x02_P7.20mm_Vertical
J5: OUT4; AMASS_XT60-F_1x02_P7.20mm_Vertical
J6: OUT5; AMASS_XT60-F_1x02_P7.20mm_Vertical

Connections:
+BATT: H4.1, H5.1, H6.1, J1.2, J2.2, J3.2, J4.2, J5.2, J6.2
GND: H1.1, H2.1, H3.1, J1.1, J2.1, J3.1, J4.1, J5.1, J6.1

Board: 2 copper layers, 12 parts (0 on the bottom side), 2 nets, no tracks yet.

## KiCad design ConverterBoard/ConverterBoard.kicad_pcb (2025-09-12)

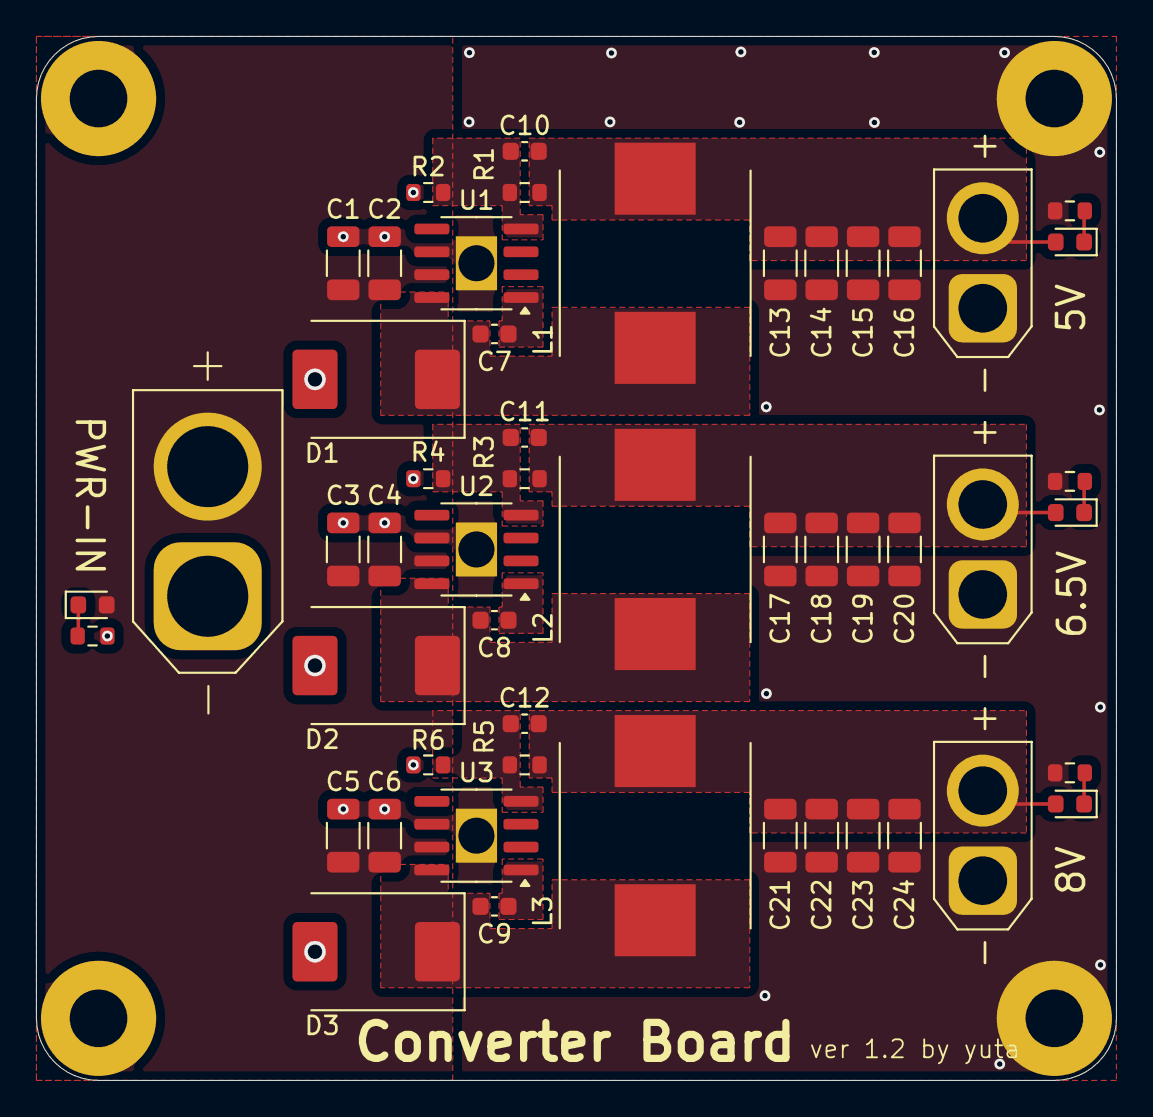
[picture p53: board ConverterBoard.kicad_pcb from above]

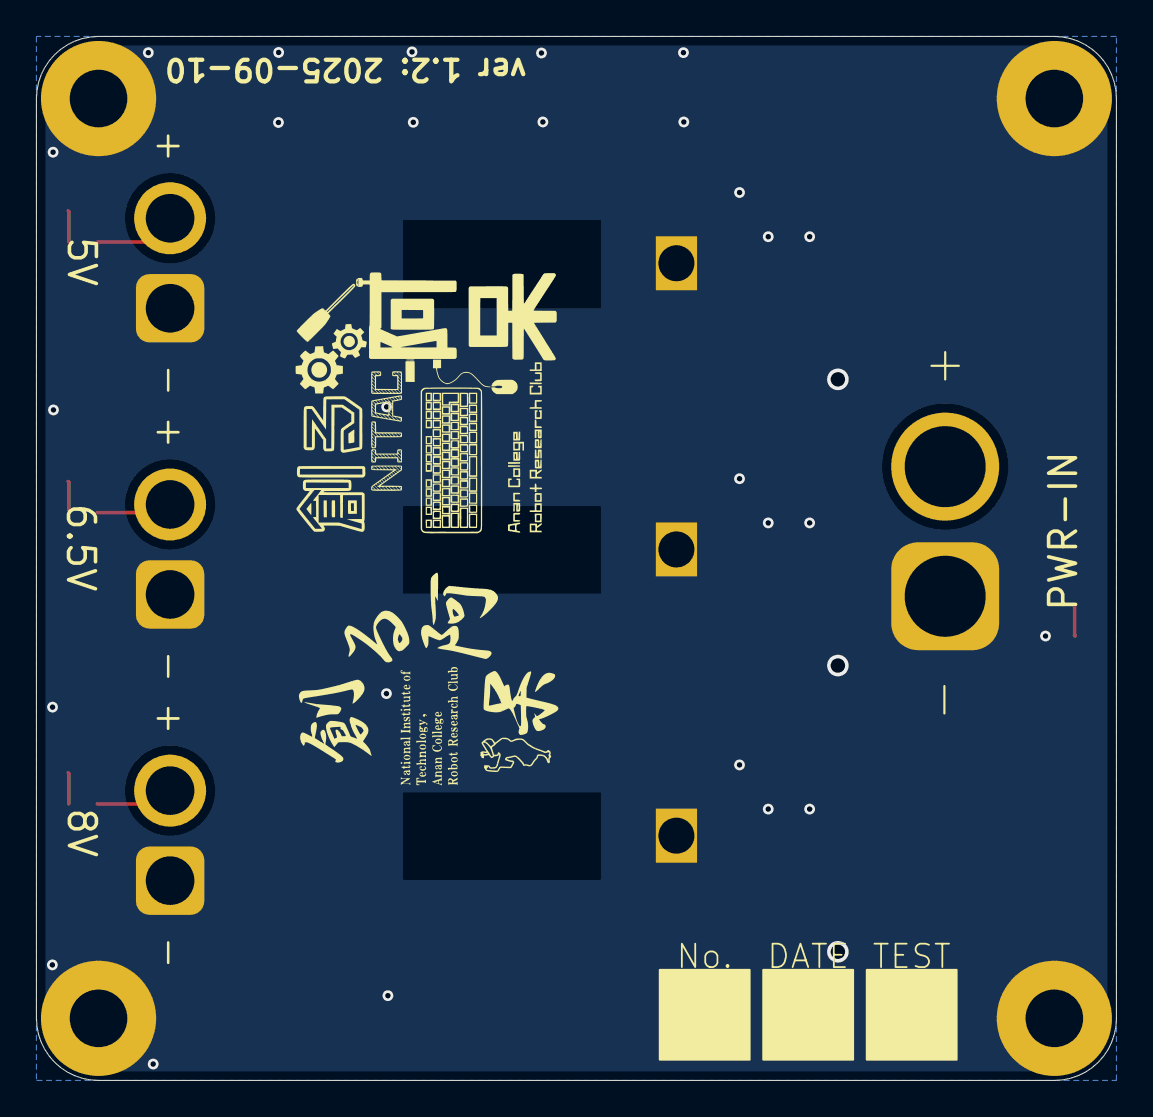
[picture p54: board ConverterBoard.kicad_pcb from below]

Board: 2 copper layers, 60.0 x 58.0 mm, 59 parts (3 on the bottom side), 18 nets.

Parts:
C1, C2, C3, C4, C5, C6: 4.7u; C_1206_3216Metric
C7, C8, C9: 10n; C_0603_1608Metric
C10, C11, C12: 82p; C_0603_1608Metric
C13, C14, C15, C16, C17, C18, C19, C20, C21, C22, C23, C24: 22u; C_1206_3216Metric
D1, D2, D3: D_Schottky; D_SMC
D4: BATT; LED_0603_1608Metric
D5: 5V; LED_0603_1608Metric
D6: 6.5V; LED_0603_1608Metric
D7: 12V; LED_0603_1608Metric
H1, H2, H3, H4: MountingHole_Pad; MountingHole_3.2mm_M3_Pad
H5: MountingHole; Title
H6: MountingHole; Info_M
H7: MountingHole; Aho_old_M
H8: MountingHole; Aho_new_M
J1: PWR_IN; AMASS_XT60-M_1x02_P7.20mm_Vertical
J2: PWR_OUT1; AMASS_XT30U-F_1x02_P5.0mm_Vertical
J3: PWR_OUT2; AMASS_XT30U-F_1x02_P5.0mm_Vertical
J4: PWR_OUT3; AMASS_XT30U-F_1x02_P5.0mm_Vertical
L1: 15u; L_Taiyo-Yuden_NR-10050_9.8x10.0mm_HandSoldering
L2, L3: 22u; L_Taiyo-Yuden_NR-10050_9.8x10.0mm_HandSoldering
R1, R3, R5: 100k; R_0603_1608Metric
R2: 31.6k; R_0603_1608Metric
R4: 22.9k; R_0603_1608Metric
R6: 18k; R_0603_1608Metric
R7: 1.5k; R_0603_1608Metric
R8: 240; R_0603_1608Metric
R9: 390; R_0603_1608Metric
R10: 500; R_0603_1608Metric
U1, U2, U3: RT6285; SOIC-8-1EP_3.9x4.9mm_P1.27mm_EP2.29x3mm_Handsoldering

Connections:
+5VA: C10.2, C13.1, C14.1, C15.1, C16.1, D5.2 (A), J2.2, L1.2, R1.1
+6.5VA: C11.2, C17.1, C18.1, C19.1, C20.1, D6.2 (A), J3.2, L2.2, R3.1
+8VA: C12.2, C21.1, C22.1, C23.1, C24.1, D7.2 (A), J4.2, L3.2, R5.1
+BATT: C1.1, C2.1, C3.1, C4.1, C5.1, C6.1, D4.2 (A), J1.2, U1.7 (VIN), U2.7 (VIN), U3.7 (VIN)
GNDA: C1.2, C2.2, C3.2, C4.2, C5.2, C6.2, C13.2, C14.2, C15.2, C16.2, C17.2, C18.2, C19.2, C20.2, C21.2, C22.2, C23.2, C24.2, D1.2 (A), D2.2 (A), D3.2 (A), H1.1, H2.1, H3.1, H4.1, J1.1, J2.1, J3.1, J4.1, R2.2, R4.2, R6.2, R7.2, R8.2, R9.2, R10.2, U1.6 (GND), U1.9 (GND), U2.6 (GND), U2.9 (GND), U3.6 (GND), U3.9 (GND)
unnamed: C7.2, D1.1 (K), L1.1, U1.8 (SW)
unnamed: C8.2, D2.1 (K), L2.1, U2.8 (SW)
unnamed: C9.2, D3.1 (K), L3.1, U3.8 (SW)
unnamed: D4.1 (K), R7.1
unnamed: D5.1 (K), R8.1
unnamed: D6.1 (K), R9.1
unnamed: D7.1 (K), R10.1
unnamed: C7.1, U1.1 (BOOT)
unnamed: C10.1, R1.2, R2.1, U1.4 (FB)
unnamed: C8.1, U2.1 (BOOT)
unnamed: C11.1, R3.2, R4.1, U2.4 (FB)
unnamed: C9.1, U3.1 (BOOT)
unnamed: C12.1, R5.2, R6.1, U3.4 (FB)

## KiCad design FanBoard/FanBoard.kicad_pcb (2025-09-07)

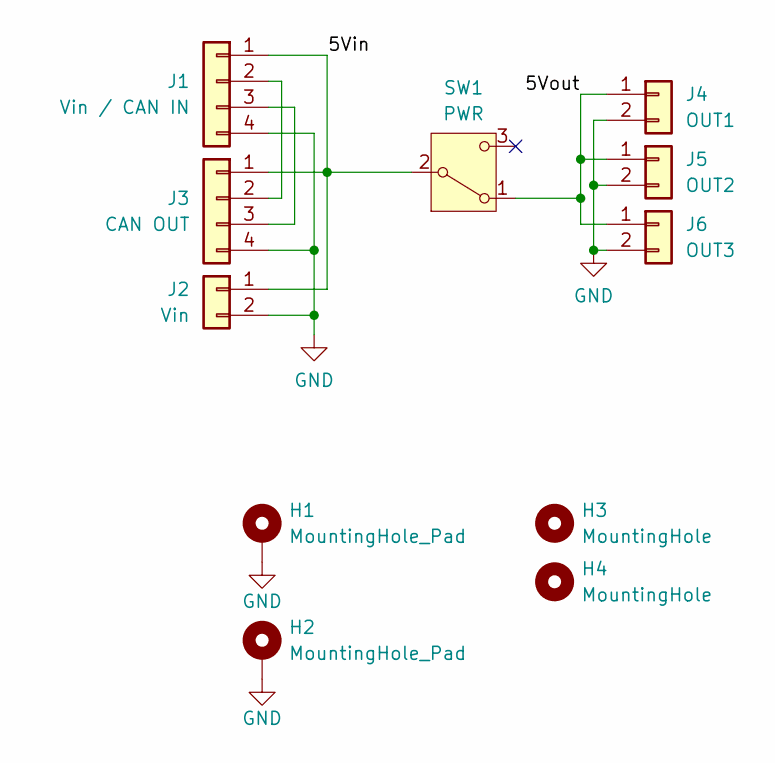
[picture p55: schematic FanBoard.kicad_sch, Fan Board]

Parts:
H1, H2: MountingHole_Pad; MountingHole_3.2mm_M3_Pad
H3: MountingHole; Title
H4: MountingHole; Info_S
J1: Vin / CAN IN; PAコネクタ(4ピンサイド型)
J2: Vin; PAコネクタ(2ピンサイド型)
J3: CAN OUT; PAコネクタ(4ピンサイド型)
J4: OUT1; PAコネクタ(2ピンサイド型)
J5: OUT2; PAコネクタ(2ピンサイド型)
J6: OUT3; PAコネクタ(2ピンサイド型)
SW1: PWR; SS-12D00G3

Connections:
/5Vin: J1.1, J2.1, J3.1, SW1.2 (B)
/5Vout: J4.1, J5.1, J6.1, SW1.1 (A)
GND: H1.1, H2.1, J1.4, J2.2, J3.4, J4.2, J5.2, J6.2
unnamed: J1.2, J3.2
unnamed: J1.3, J3.3

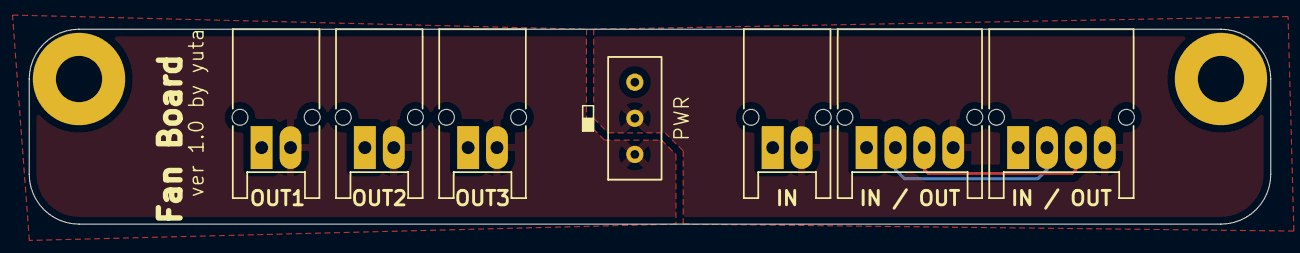
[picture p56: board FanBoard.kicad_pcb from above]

Board: 2 copper layers, 86.0 x 13.5 mm, 11 parts (1 on the bottom side), 5 nets.

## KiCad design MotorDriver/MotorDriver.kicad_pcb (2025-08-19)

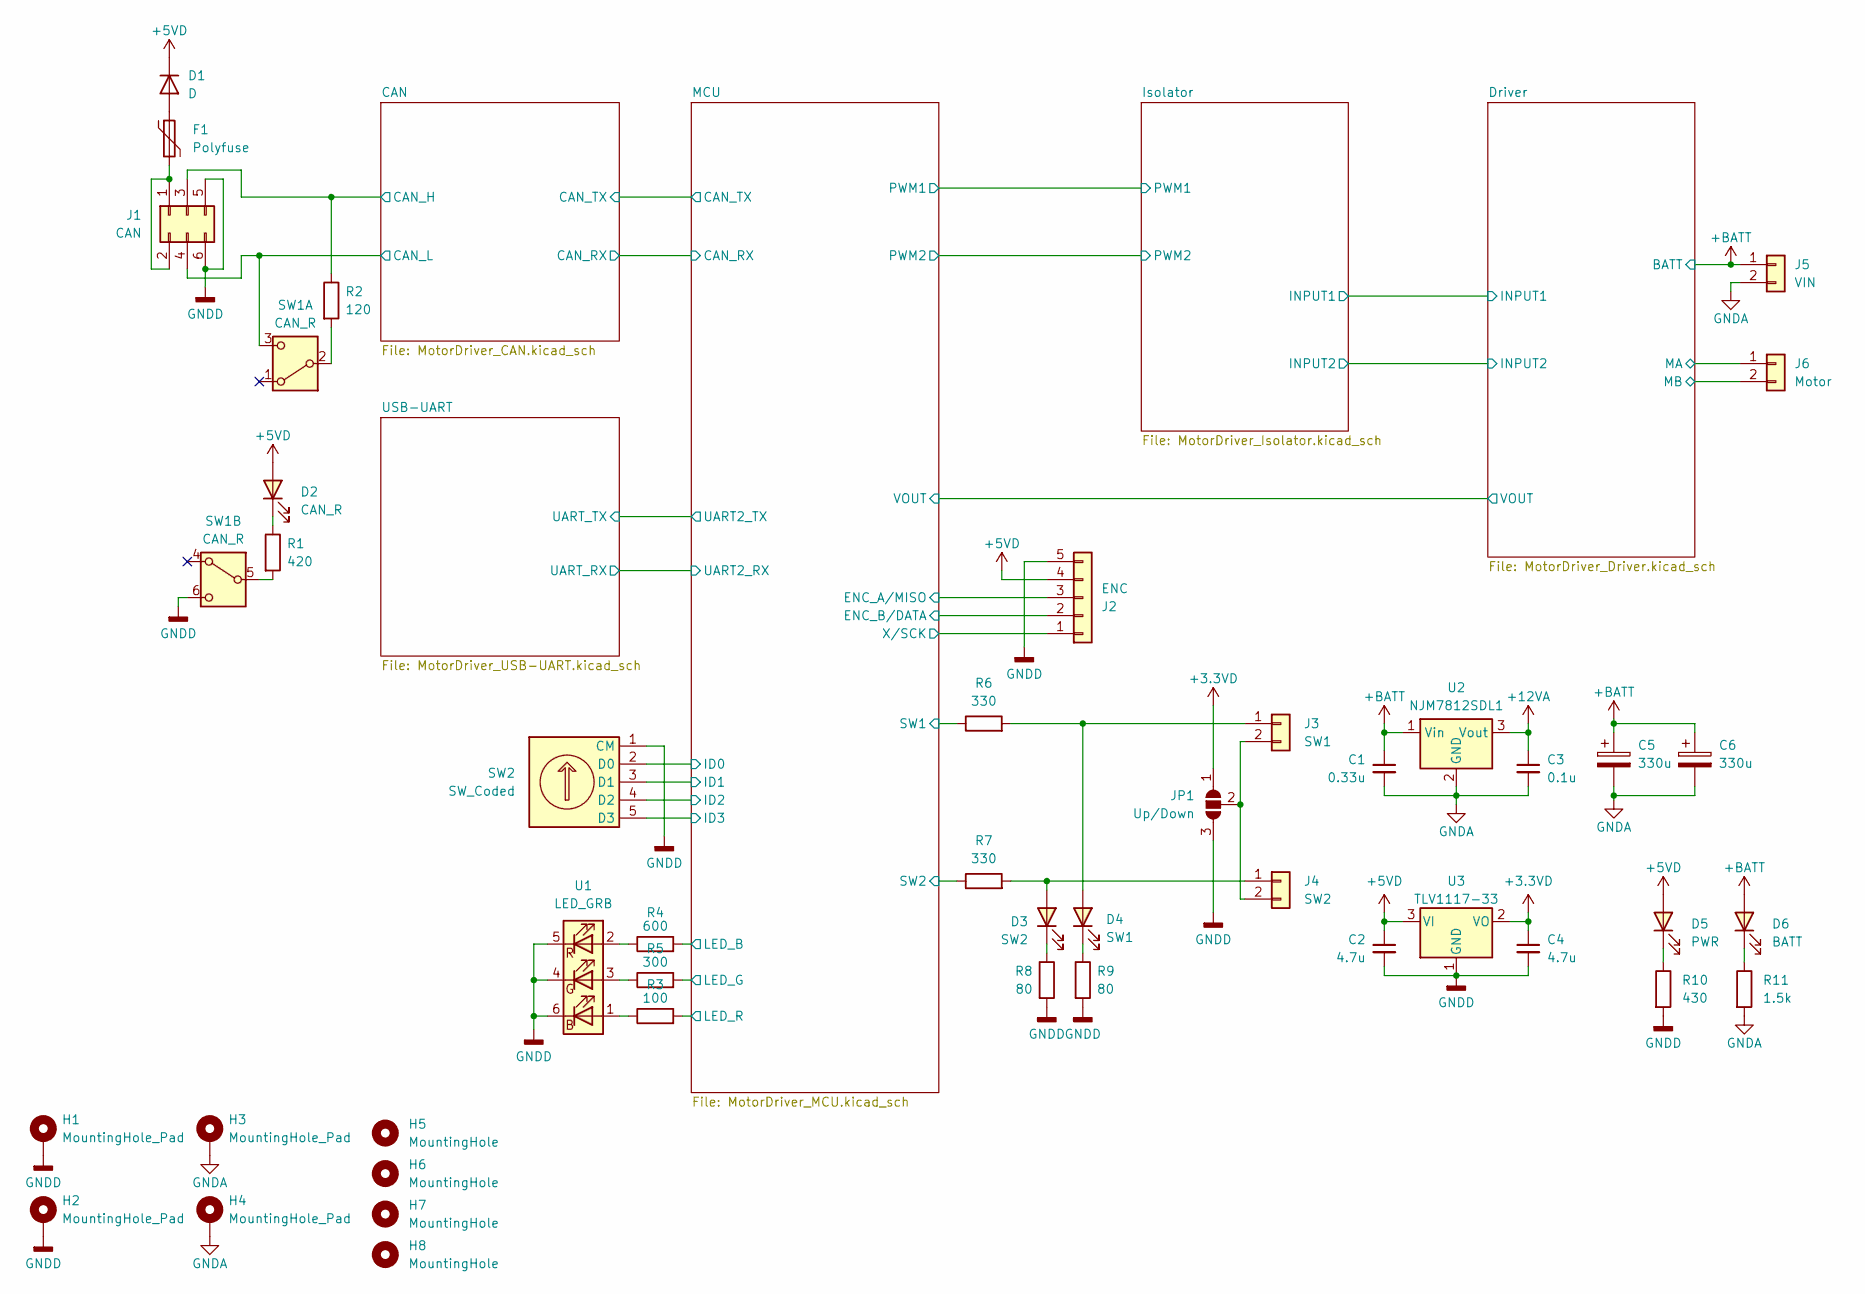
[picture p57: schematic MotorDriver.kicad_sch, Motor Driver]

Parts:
C1: 0.33u; C_0603_1608Metric
C2, C4: 4.7u; C_0603_1608Metric
C3: 0.1u; C_0603_1608Metric
C5, C6: 330u; CP_Elec_10x10.5
D1: D; Nexperia_CFP3_SOD-123W
D2: CAN_R; LED_0603_1608Metric
D3: SW2; LED_0603_1608Metric
D4: SW1; LED_0603_1608Metric
D5: PWR; LED_0603_1608Metric
D6: BATT; LED_0603_1608Metric
F1: Polyfuse; MF-FSMF
H1, H2, H3, H4: MountingHole_Pad; MountingHole_3.2mm_M3_Pad
H5: MountingHole; Title
H6: MountingHole; Aho_old_S
H7: MountingHole; Aho_new_S
H8: MountingHole; Info_M_3
J1: CAN; IDC-Header_2x03_P2.54mm_Horizontal
J2: ENC; SM05B-PASS-TBx
J3: SW1; SM02B-PASS-TBx
J4: SW2; SM02B-PASS-TBx
J5: VIN; XT60PW-M_Horizontal
J6: Motor; XT60PW-F_Horizontal
JP1: Up/Down; SolderJumper-3_P1.3mm_Open_Pad1.0x1.5mm
R1: 420; R_0603_1608Metric
R2: 120; R_0603_1608Metric
R3: 100; R_0603_1608Metric
R4: 600; R_0603_1608Metric
R5: 300; R_0603_1608Metric
R6, R7: 330; R_0603_1608Metric
R8, R9: 80; R_0603_1608Metric
R10: 430; R_0603_1608Metric
R11: 1.5k; R_0603_1608Metric
SW1: CAN_R; SLW
SW2: SW_Coded; RDS-1055-SMT
U1: LED_GRB; LED_ROHM_SMLVN6
U2: NJM7812SDL1; TO-252-2
U3: TLV1117-33; SOT-223-3_TabPin2

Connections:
+3.3VD: C4.1, JP1.1 (A), U3.2 (VO); also elsewhere on the board
+5VD: C2.1, D1.1 (K), D2.2 (A), D5.2 (A), J2.4, U3.3 (VI); also elsewhere on the board
+12VA: C3.1, U2.3 (Vout); also elsewhere on the board
+BATT: C1.1, C5.1, C6.1, D6.2 (A), J5.1, U2.1 (Vin); also elsewhere on the board
/CAN/CAN_H: J1.3, R2.1; also elsewhere on the board
/CAN/CAN_L: J1.4, SW1.3 (C); also elsewhere on the board
/Driver/MB: J6.2; also elsewhere on the board
/MCU/ENC_A/MISO: J2.3; also elsewhere on the board
/MCU/ENC_B/DATA: J2.2; also elsewhere on the board
/MCU/ID0: SW2.2 (D0); also elsewhere on the board
/MCU/ID1: SW2.3 (D1); also elsewhere on the board
/MCU/ID2: SW2.4 (D2); also elsewhere on the board
/MCU/ID3: SW2.5 (D3); also elsewhere on the board
/MCU/LED_B: R4.2; also elsewhere on the board
/MCU/LED_G: R5.2; also elsewhere on the board
/MCU/LED_R: R3.2; also elsewhere on the board
/MCU/SW1: R6.1; also elsewhere on the board
/MCU/SW2: R7.1; also elsewhere on the board
/MCU/X/SCK: J2.1; also elsewhere on the board
CS-: J6.1; also elsewhere on the board
GNDA: C1.2, C3.2, C5.2, C6.2, H3.1, H4.1, J5.2, R11.2, U2.2 (GND); also elsewhere on the board
GNDD: C2.2, C4.2, H1.1, H2.1, J1.5, J1.6, J2.5, JP1.3 (B), R8.2, R9.2, R10.2, SW1.6 (C), SW2.1 (CM), U1.4, U1.5, U1.6, U3.1 (GND); also elsewhere on the board
unnamed: D1.2 (A), F1.1
unnamed: D2.1 (K), R1.1
unnamed: D3.2 (A), J4.1, R7.2
unnamed: D3.1 (K), R8.1
unnamed: D4.2 (A), J3.1, R6.2
unnamed: D4.1 (K), R9.1
unnamed: D5.1 (K), R10.1
unnamed: D6.1 (K), R11.1
unnamed: F1.2, J1.1, J1.2
unnamed: J3.2, J4.2, JP1.2 (C)
unnamed: R3.1, U1.1
unnamed: R4.1, U1.2
unnamed: R5.1, U1.3
unnamed: R2.2, SW1.2 (B)
unnamed: R1.2, SW1.5 (B)

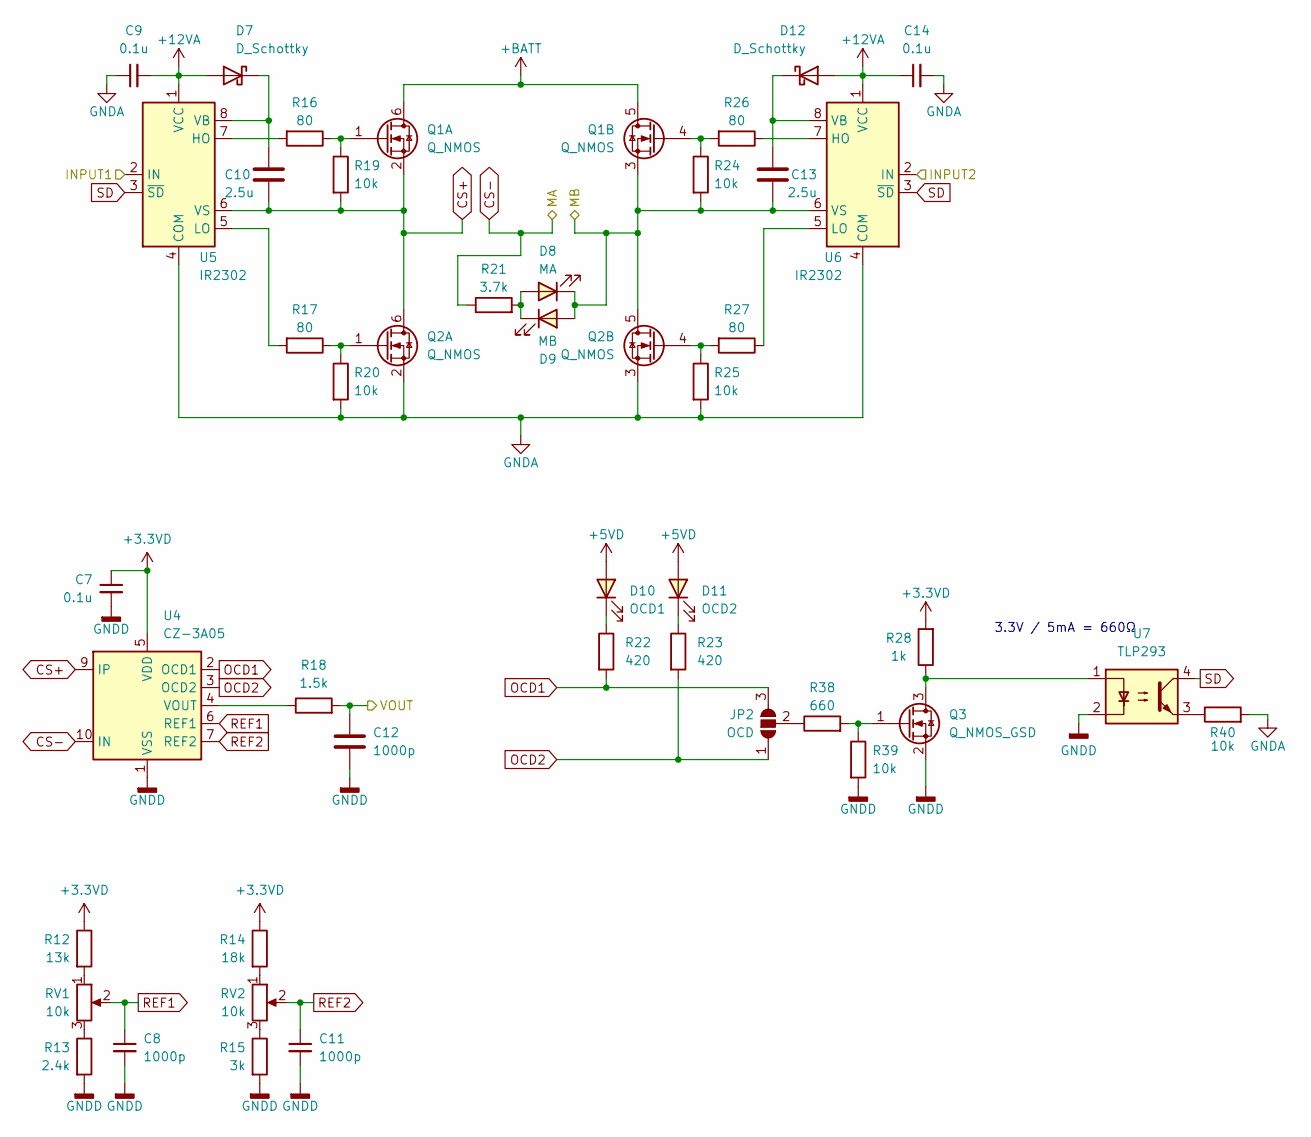
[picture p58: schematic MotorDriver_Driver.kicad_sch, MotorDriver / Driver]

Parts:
C7, C9, C14: 0.1u; C_0603_1608Metric
C8, C11, C12: 1000p; C_0603_1608Metric
C10, C13: 2.5u; C_0603_1608Metric
D7, D12: D_Schottky; D_SOD-123
D8: MA; LED_0603_1608Metric
D9: MB; LED_0603_1608Metric
D10: OCD1; LED_0603_1608Metric
D11: OCD2; LED_0603_1608Metric
JP2: OCD; SolderJumper-3_P1.3mm_Open_Pad1.0x1.5mm
Q1, Q2: Q_NMOS; Vishay_PowerPAK_8x8L_Dual
Q3: Q_NMOS_GSD; TSOT-23
R12: 13k; R_0603_1608Metric
R13: 2.4k; R_0603_1608Metric
R14: 18k; R_0603_1608Metric
R15: 3k; R_0603_1608Metric
R16, R17, R26, R27: 80; R_0603_1608Metric
R18: 1.5k; R_0603_1608Metric
R19, R20, R24, R25, R39, R40: 10k; R_0603_1608Metric
R21: 3.7k; R_0603_1608Metric
R22, R23: 420; R_0603_1608Metric
R28: 1k; R_0603_1608Metric
R38: 660; R_0603_1608Metric
RV1, RV2: 10k; ST-4ETB103
U4: CZ-3A05; CZ3A
U5, U6: IR2302; SOIC-8_3.9x4.9mm_P1.27mm
U7: TLP293; SOIC-4_4.55x2.6mm_P1.27mm

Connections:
+3.3VD: C7.1, R12.1, R14.1, R28.2, U4.5 (VDD); also elsewhere on the board
+5VD: D10.2 (A), D11.2 (A); also elsewhere on the board
+12VA: C9.2, C14.1, D7.2 (A), D12.2 (A), U5.1 (VCC), U6.1 (VCC); also elsewhere on the board
+BATT: Q1.5 (D), Q1.6 (D); also elsewhere on the board
/Driver/INPUT1: U5.2 (IN); also elsewhere on the board
/Driver/INPUT2: U6.2 (IN); also elsewhere on the board
/Driver/MB: C13.2, D8.1 (K), D9.2 (A), Q1.3 (S), Q2.5 (D), R24.2, U6.6 (VS); also elsewhere on the board
/Driver/VOUT: C12.1, R18.2; also elsewhere on the board
CS+: C10.2, Q1.2 (S), Q2.6 (D), R19.2, U4.9 (IP), U5.6 (VS)
CS-: R21.1, U4.10 (IN); also elsewhere on the board
GNDA: C9.1, C14.2, Q2.2 (S), Q2.3 (S), R20.2, R25.2, R40.2, U5.4 (COM), U6.4 (COM); also elsewhere on the board
GNDD: C7.2, C8.2, C11.2, C12.2, Q3.2 (S), R13.2, R15.2, R39.2, U4.1 (VSS), U4.8 (VSS), U7.2; also elsewhere on the board
unnamed: C10.1, D7.1 (K), U5.8 (VB)
unnamed: D8.2 (A), D9.1 (K), R21.2
unnamed: D10.1 (K), R22.1
unnamed: D11.1 (K), R23.1
unnamed: C13.1, D12.1 (K), U6.8 (VB)
unnamed: JP2.2 (C), R38.1
unnamed: Q1.1 (G), R16.1, R19.1
unnamed: Q1.4 (G), R24.1, R26.2
unnamed: Q2.1 (G), R17.1, R20.1
unnamed: Q2.4 (G), R25.1, R27.2
unnamed: Q3.3 (D), R28.1, U7.1
unnamed: Q3.1 (G), R38.2, R39.1
unnamed: R12.2, RV1.1
unnamed: R13.1, RV1.3
unnamed: R14.2, RV2.1
unnamed: R15.1, RV2.3
unnamed: R40.1, U7.3
unnamed: R18.1, U4.4 (VOUT)
unnamed: R16.2, U5.7 (HO)
unnamed: R17.2, U5.5 (LO)
unnamed: R26.1, U6.7 (HO)
unnamed: R27.1, U6.5 (LO)
OCD1: JP2.3 (B), R22.2, U4.2 (OCD1)
OCD2: JP2.1 (A), R23.2, U4.3 (OCD2)
REF1: C8.1, RV1.2, U4.6 (REF1)
REF2: C11.1, RV2.2, U4.7 (REF2)
SD: U5.3 (~SD), U6.3 (~SD), U7.4

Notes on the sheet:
3.3V / 5mA = 660Ω

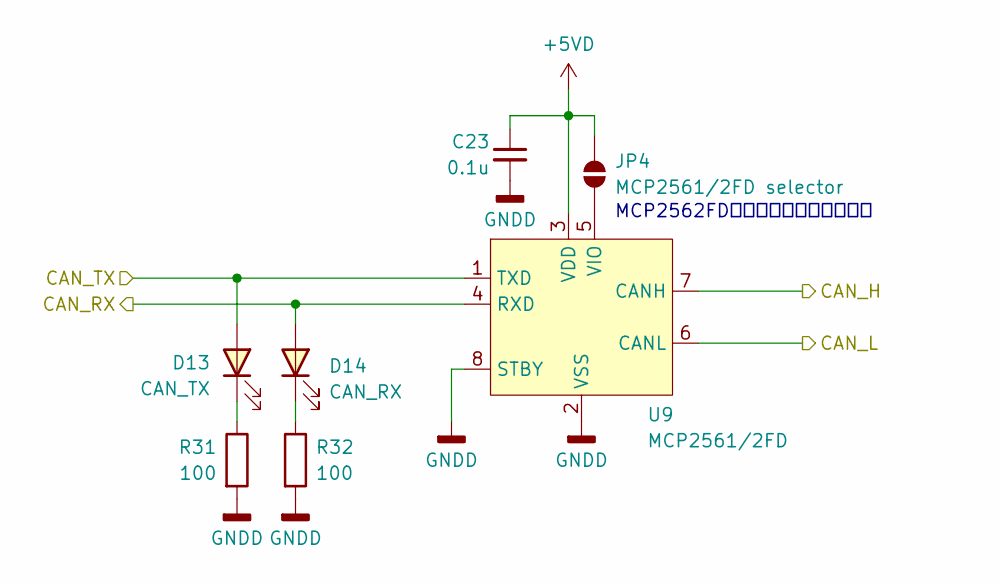
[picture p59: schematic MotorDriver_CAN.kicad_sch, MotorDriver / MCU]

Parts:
C23: 0.1u; C_0603_1608Metric
D13: CAN_TX; LED_0603_1608Metric
D14: CAN_RX; LED_0603_1608Metric
JP4: MCP2561/2FD selector; SolderJumper-2_P1.3mm_Open_Pad1.0x1.5mm
R31, R32: 100; R_0603_1608Metric
U9: MCP2561/2FD; SOIC-8_3.9x4.9mm_P1.27mm

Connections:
+5VD: C23.1, JP4.2 (B), U9.3 (VDD); also elsewhere on the board
/CAN/CAN_H: U9.7 (CANH); also elsewhere on the board
/CAN/CAN_L: U9.6 (CANL); also elsewhere on the board
/CAN/CAN_RX: D14.2 (A), U9.4 (RXD); also elsewhere on the board
/CAN/CAN_TX: D13.2 (A), U9.1 (TXD); also elsewhere on the board
GNDD: C23.2, R31.2, R32.2, U9.2 (VSS), U9.8 (STBY); also elsewhere on the board
unnamed: D13.1 (K), R31.1
unnamed: D14.1 (K), R32.1
unnamed: JP4.1 (A), U9.5 (VIO)

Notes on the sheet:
MCP2562FDを使うならジャンパする

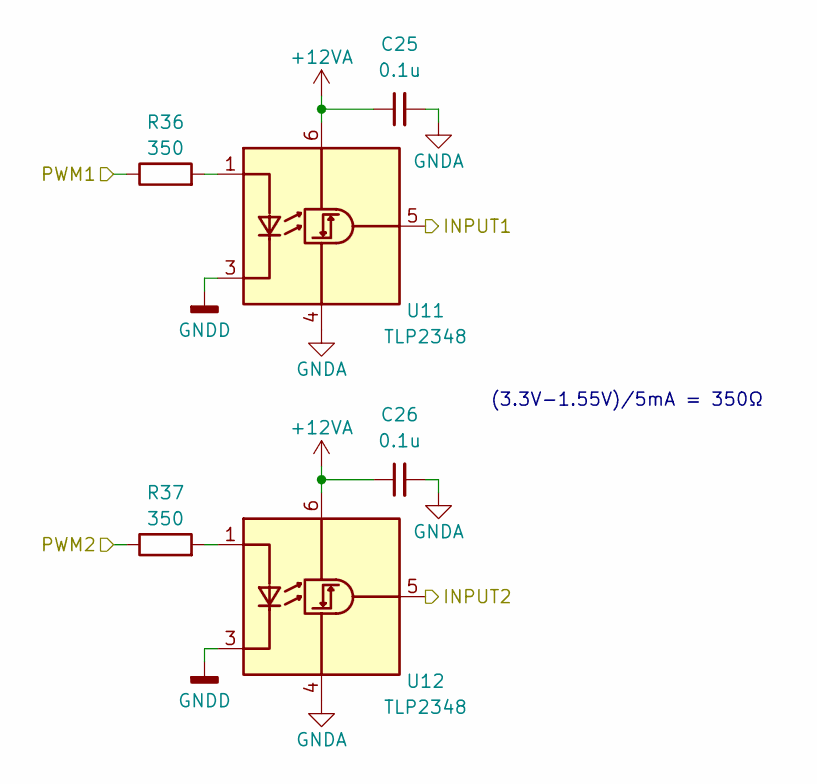
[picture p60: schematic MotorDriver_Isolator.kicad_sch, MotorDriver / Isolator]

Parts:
C25, C26: 0.1u; C_0603_1608Metric
R36, R37: 350; R_0603_1608Metric
U11, U12: TLP2348; SO-5-6_4.55x3.7mm_P1.27mm

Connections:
+12VA: C25.1, C26.1, U11.6 (VDD), U12.6 (VDD); also elsewhere on the board
/Driver/INPUT1: U11.5 (VO); also elsewhere on the board
/Driver/INPUT2: U12.5 (VO); also elsewhere on the board
/Isolator/PWM1: R36.1; also elsewhere on the board
/Isolator/PWM2: R37.1; also elsewhere on the board
GNDA: C25.2, C26.2, U11.4 (GND), U12.4 (GND); also elsewhere on the board
GNDD: U11.3 (K), U12.3 (K); also elsewhere on the board
unnamed: R36.2, U11.1 (A)
unnamed: R37.2, U12.1 (A)

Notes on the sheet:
(3.3V-1.55V)/5mA = 350Ω


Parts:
C15, C19, C20, C21: 0.1u; C_0603_1608Metric
C16, C17: 15p; C_0603_1608Metric
C18: 4.7u; C_0603_1608Metric
C22: 1u; C_0603_1608Metric
FB1: FerriteBead; L_0603_1608Metric
J7: SWD; JST_SH_SM04B-SRSS-TB_1x04-1MP_P1.00mm_Horizontal
R29: 10k; R_0603_1608Metric; not fitted
R30: 10k; R_0603_1608Metric
SW3: RESET; TVAF06-A020B-R
U8: STM32F303K8Tx; LQFP-32_7x7mm_P0.8mm
Y1: Crystal_GND2; XRCGB

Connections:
+3.3VADC: C21.1, C22.1, FB1.2, U8.5 (VDDA)
+3.3VD: C18.1, C19.1, C20.1, FB1.1, R29.1, U8.1 (VDD), U8.17 (VDD); also elsewhere on the board
/CAN/CAN_RX: U8.21 (PA11); also elsewhere on the board
/CAN/CAN_TX: U8.22 (PA12); also elsewhere on the board
/Driver/VOUT: U8.10 (PA4); also elsewhere on the board
/Isolator/PWM1: U8.14 (PB0); also elsewhere on the board
/Isolator/PWM2: U8.15 (PB1); also elsewhere on the board
/MCU/ENC_A/MISO: U8.18 (PA8); also elsewhere on the board
/MCU/ENC_B/DATA: U8.19 (PA9); also elsewhere on the board
/MCU/ID0: U8.27 (PB4); also elsewhere on the board
/MCU/ID1: U8.29 (PB6); also elsewhere on the board
/MCU/ID2: U8.28 (PB5); also elsewhere on the board
/MCU/ID3: U8.30 (PB7); also elsewhere on the board
/MCU/LED_B: U8.8 (PA2); also elsewhere on the board
/MCU/LED_G: U8.7 (PA1); also elsewhere on the board
/MCU/LED_R: U8.6 (PA0); also elsewhere on the board
/MCU/NRST: C15.1, J7.4, SW3.2, U8.4 (NRST)
/MCU/SW1: U8.12 (PA6); also elsewhere on the board
/MCU/SW2: U8.13 (PA7); also elsewhere on the board
/MCU/SWCLK: J7.2, U8.24 (PA14)
/MCU/SWDIO: J7.1, U8.23 (PA13)
/MCU/UART2_RX: U8.25 (PA15); also elsewhere on the board
/MCU/UART2_TX: U8.26 (PB3); also elsewhere on the board
/MCU/X/SCK: U8.11 (PA5); also elsewhere on the board
GNDD: C15.2, C16.2, C17.2, C18.2, C19.2, C20.2, C21.2, C22.2, J7.3, R30.2, SW3.1, U8.16 (VSS), U8.32 (VSS); also elsewhere on the board
unnamed: R29.2, R30.1, U8.31 (BOOT0)
unnamed: C16.1, U8.2 (PF0), Y1.1
unnamed: C17.1, U8.3 (PF1), Y1.3

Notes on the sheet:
PWM1: PB0: TIM3_CH3 PWM2: PB1: TIM3_CH4 ENC_A: PA8: TIM1_CH1 ENC_B: PA9: TIM1_CH2 VOUT: PA4: ADC2_IN1 LED_R: PA0: TIM2_CH1 LED_G: PA1: TIM2_CH2 LED_B: PA2: TIM2_CH3 UART2_TX: PB3 UART2_RX: PA15


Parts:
C24: 0.1u; C_0603_1608Metric
D15: D; Nexperia_CFP3_SOD-123W
D16: DATA; LED_0603_1608Metric
F2: Polyfuse; MF-FSMF
J8: Debug; USB_C_Receptacle_GCT_USB4105-xx-A_16P_TopMnt_Horizontal
R33, R34: 5.1k; R_0603_1608Metric
R35: 100; R_0603_1608Metric
U10: CH340E; MSOP-10_3x3mm_P0.5mm

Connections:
+3.3VD: C24.1, U10.7 (VCC), U10.10 (V3); also elsewhere on the board
+5VD: F2.1; also elsewhere on the board
/MCU/UART2_RX: U10.8 (TXD); also elsewhere on the board
/MCU/UART2_TX: U10.9 (RXD); also elsewhere on the board
GNDD: C24.2, J8.A1 (GND), J8.A12 (GND), J8.B1 (GND), J8.B12 (GND), R33.2, R34.2, R35.2, U10.3 (GND); also elsewhere on the board
unnamed: D15.2 (A), J8.A4 (VBUS), J8.A9 (VBUS), J8.B4 (VBUS), J8.B9 (VBUS)
unnamed: D15.1 (K), F2.2
unnamed: D16.2 (A), U10.6 (TNOW)
unnamed: D16.1 (K), R35.1
unnamed: J8.A5 (CC1), R34.1
unnamed: J8.B5 (CC2), R33.1
unnamed: J8.A6 (D+), J8.B6 (D+), U10.1 (UD+)
unnamed: J8.A7 (D-), J8.B7 (D-), U10.2 (UD-)

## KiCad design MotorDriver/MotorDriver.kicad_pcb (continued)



Board: 4 copper layers, 70.0 x 45.0 mm, 125 parts (69 on the bottom side), 94 nets.

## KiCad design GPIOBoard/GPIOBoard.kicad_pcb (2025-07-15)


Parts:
C1, C2: 4.7u; C_0603_1608Metric
D1, D2, D3, D4, D5, D6, D7, D8: LED; LED_0603_1608Metric
D9: TX; LED_0603_1608Metric
D10: RX; LED_0603_1608Metric
D11: PWR; LED_0603_1608Metric
D16: D; Nexperia_CFP3_SOD-123W
D17: CAN_R; LED_0603_1608Metric
F1: Polyfuse; MF-FSMF
H1, H2, H3, H4: MountingHole_Pad; MountingHole_3.2mm_M3_Pad
J1: GPIO1; PAコネクタ(3ピンサイド型)
J2: GPIO2; PAコネクタ(3ピンサイド型)
J3: GPIO3; PAコネクタ(3ピンサイド型)
J4: GPIO4; PAコネクタ(3ピンサイド型)
J5: GPIO5; PAコネクタ(3ピンサイド型)
J6: GPIO6; PAコネクタ(3ピンサイド型)
J7: GPIO7; PAコネクタ(3ピンサイド型)
J8: GPIO8; PAコネクタ(3ピンサイド型)
J9: IMU; PAコネクタ(4ピンサイド型)
J12: CAN; IDC-Header_2x03_P2.54mm_Horizontal
R1, R2, R3, R4, R5, R6, R7, R8: 80; R_0603_1608Metric
R9, R10, R11, R12, R13, R14, R15, R16: 330; R_0603_1608Metric
R17, R18: 96; R_0603_1608Metric
R19: 430; R_0603_1608Metric
R25: 120; R_0603_1608Metric
R27: 420; R_0603_1608Metric
R28: 100; R_0603_1608Metric
R29: 600; R_0603_1608Metric
R30: 300; R_0603_1608Metric
SW2: SW_Coded; RDS-1055-SMT
SW3: CAN_R; SLW
U2: TLV1117-33; SOT-223-3_TabPin2
U5: LED_GRB; LED_ROHM_SMLVN6

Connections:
+3.3V: C2.1, J1.1, J2.1, J3.1, J4.1, J5.1, J6.1, J7.1, J8.1, U2.2 (VO); also elsewhere on the board
+5V: C1.1, D11.2 (A), D16.1 (K), D17.2 (A), J9.1, U2.3 (VI); also elsewhere on the board
/CAN/CAN_H: J12.3, R25.1; also elsewhere on the board
/CAN/CAN_L: J12.4, SW3.1 (A); also elsewhere on the board
/MCU/GPIO1: R9.2; also elsewhere on the board
/MCU/GPIO2: R10.2; also elsewhere on the board
/MCU/GPIO3: R11.2; also elsewhere on the board
/MCU/GPIO4: R12.2; also elsewhere on the board
/MCU/GPIO5: R13.2; also elsewhere on the board
/MCU/GPIO6: R14.2; also elsewhere on the board
/MCU/GPIO7: R15.2; also elsewhere on the board
/MCU/GPIO8: R16.2; also elsewhere on the board
/MCU/ID0: SW2.2 (D0); also elsewhere on the board
/MCU/ID1: SW2.3 (D1); also elsewhere on the board
/MCU/ID2: SW2.4 (D2); also elsewhere on the board
/MCU/ID3: SW2.5 (D3); also elsewhere on the board
/MCU/LED_B: R28.2; also elsewhere on the board
/MCU/LED_G: R30.2; also elsewhere on the board
/MCU/LED_R: R29.2; also elsewhere on the board
/MCU/UART1_RX: D10.2 (A), J9.3; also elsewhere on the board
/MCU/UART1_TX: D9.2 (A), J9.2; also elsewhere on the board
GNDD: C1.2, C2.2, H1.1, H2.1, H3.1, H4.1, J1.3, J2.3, J3.3, J4.3, J5.3, J6.3, J7.3, J8.3, J9.4, J12.5, J12.6, R1.2, R2.2, R3.2, R4.2, R5.2, R6.2, R7.2, R8.2, R17.2, R18.2, R19.2, SW2.1 (CM), SW3.4 (A), U2.1 (GND), U5.4, U5.5, U5.6; also elsewhere on the board
unnamed: D1.2 (A), J1.2, R9.1
unnamed: D1.1 (K), R1.1
unnamed: D2.2 (A), J2.2, R10.1
unnamed: D2.1 (K), R2.1
unnamed: D3.2 (A), J3.2, R11.1
unnamed: D3.1 (K), R3.1
unnamed: D4.2 (A), J4.2, R12.1
unnamed: D4.1 (K), R4.1
unnamed: D5.2 (A), J5.2, R13.1
unnamed: D5.1 (K), R5.1
unnamed: D6.2 (A), J6.2, R14.1
unnamed: D6.1 (K), R6.1
unnamed: D7.2 (A), J7.2, R15.1
unnamed: D7.1 (K), R7.1
unnamed: D8.2 (A), J8.2, R16.1
unnamed: D8.1 (K), R8.1
unnamed: D9.1 (K), R17.1
unnamed: D10.1 (K), R18.1
unnamed: D11.1 (K), R19.1
unnamed: D16.2 (A), F1.1
unnamed: D17.1 (K), R27.1
unnamed: F1.2, J12.1, J12.2
unnamed: R28.1, U5.1
unnamed: R29.1, U5.2
unnamed: R30.1, U5.3
unnamed: R25.2, SW3.2 (B)
unnamed: R27.2, SW3.5 (B)

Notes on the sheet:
Vcc = 3.3V Vf = 2.1V, If = 12.5mA (3.3-2.1) / 0.0125 = 96Ω
Vcc = 5.0V Vf = 2.2V, If = 6.5mA (5.0-2.2) / 0.0065 = 430Ω
終端抵抗の接続切り替え
Vcc = 3.3V Vf = 2.9V, If = 5mA (3.3-2.9) / 0.005 = 80Ω
LEDの色 電源：オレンジ 通信：緑 その他：青
Vcc = 5V Vf = 2.9V, If = 5mA (5 - 2.9) / 0.005 = 420Ω


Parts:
C11: 0.1u; C_0603_1608Metric
D12: Data; LED_0603_1608Metric
D15: D; Nexperia_CFP3_SOD-123W
F2: Polyfuse; MF-FSMF
J10: Debug; USB_C_Receptacle_GCT_USB4105-xx-A_16P_TopMnt_Horizontal
R20: 96; R_0603_1608Metric
R21, R22: 5.1k; R_0603_1608Metric
U3: CH340E; MSOP-10_3x3mm_P0.5mm

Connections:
+3.3V: C11.1, U3.7 (VCC), U3.10 (V3); also elsewhere on the board
+5V: D15.1 (K); also elsewhere on the board
/MCU/UART2_RX: U3.8 (TXD); also elsewhere on the board
/MCU/UART2_TX: U3.9 (RXD); also elsewhere on the board
GNDD: C11.2, J10.A1 (GND), J10.A12 (GND), J10.B1 (GND), J10.B12 (GND), R20.2, R21.2, R22.2, U3.3 (GND); also elsewhere on the board
unnamed: D12.2 (A), U3.6 (TNOW)
unnamed: D12.1 (K), R20.1
unnamed: D15.2 (A), F2.1
unnamed: F2.2, J10.A4 (VBUS), J10.A9 (VBUS), J10.B4 (VBUS), J10.B9 (VBUS)
unnamed: J10.A5 (CC1), R22.1
unnamed: J10.B5 (CC2), R21.1
unnamed: J10.A6 (D+), J10.B6 (D+), U3.1 (UD+)
unnamed: J10.A7 (D-), J10.B7 (D-), U3.2 (UD-)

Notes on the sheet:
Vcc = 3.3V Vf = 2.1V, If = 12.5mA (3.3-2.1) / 0.0125 = 96Ω


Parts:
C3, C4, C6, C8: 0.1u; C_0603_1608Metric
C5: 4.7u; C_0603_1608Metric
C7: 1u; C_0603_1608Metric
C9, C10: 15p; C_0603_1608Metric
FB1: FerriteBead; L_0603_1608Metric
J11: SWD; JST_SH_SM04B-SRSS-TB_1x04-1MP_P1.00mm_Horizontal
R26: 10k; R_0603_1608Metric
R31: 10k; R_0603_1608Metric; not fitted
SW1: RESET; TVAF06-A020B-R
U1: STM32F303K8Tx; LQFP-32_7x7mm_P0.8mm
Y1: Crystal_GND2; XRCGB

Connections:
+3.3V: C3.1, C4.1, C5.1, FB1.1, R31.1, U1.1 (VDD), U1.17 (VDD); also elsewhere on the board
+3.3VA: C6.1, C7.1, FB1.2, U1.5 (VDDA)
/CAN/CAN_RX: U1.21 (PA11); also elsewhere on the board
/CAN/CAN_TX: U1.22 (PA12); also elsewhere on the board
/MCU/GPIO1: U1.15 (PB1); also elsewhere on the board
/MCU/GPIO2: U1.14 (PB0); also elsewhere on the board
/MCU/GPIO3: U1.13 (PA7); also elsewhere on the board
/MCU/GPIO4: U1.12 (PA6); also elsewhere on the board
/MCU/GPIO5: U1.11 (PA5); also elsewhere on the board
/MCU/GPIO6: U1.9 (PA3); also elsewhere on the board
/MCU/GPIO7: U1.8 (PA2); also elsewhere on the board
/MCU/GPIO8: U1.7 (PA1); also elsewhere on the board
/MCU/ID0: U1.27 (PB4); also elsewhere on the board
/MCU/ID1: U1.29 (PB6); also elsewhere on the board
/MCU/ID2: U1.28 (PB5); also elsewhere on the board
/MCU/ID3: U1.30 (PB7); also elsewhere on the board
/MCU/LED_B: U1.6 (PA0); also elsewhere on the board
/MCU/LED_G: U1.18 (PA8); also elsewhere on the board
/MCU/LED_R: U1.10 (PA4); also elsewhere on the board
/MCU/NRST: C8.1, J11.4, SW1.2, U1.4 (NRST)
/MCU/SWCLK: J11.2, U1.24 (PA14)
/MCU/SWDIO: J11.1, U1.23 (PA13)
/MCU/UART1_RX: U1.20 (PA10); also elsewhere on the board
/MCU/UART1_TX: U1.19 (PA9); also elsewhere on the board
/MCU/UART2_RX: U1.25 (PA15); also elsewhere on the board
/MCU/UART2_TX: U1.26 (PB3); also elsewhere on the board
GNDD: C3.2, C4.2, C5.2, C6.2, C7.2, C8.2, C9.2, C10.2, J11.3, R26.2, SW1.1, U1.16 (VSS), U1.32 (VSS); also elsewhere on the board
unnamed: R26.1, R31.2, U1.31 (BOOT0)
unnamed: C9.1, U1.2 (PF0), Y1.1
unnamed: C10.1, U1.3 (PF1), Y1.3

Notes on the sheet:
GPIO1: PB1: TIM3_CH4 GPIO2: PB0: TIM3_CH3 GPIO3: PA7: TIM3_CH2 GPIO4: PA6: TIM3_CH1 GPIO5: PA5: TIM2_CH1 GPIO6: PA3: TIM2_CH4 GPIO7: PA2: TIM2_CH3 GPIO8: PA1: TIM2_CH2 PA9: USART1_TX PA10: USART1_RX PB3: USART2_TX PA15: USART2_RX


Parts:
C12: 0.1u; C_0603_1608Metric
D13: CAN_TX; LED_0603_1608Metric
D14: CAN_RX; LED_0603_1608Metric
JP1: MCP2561/2FD selector; SolderJumper-2_P1.3mm_Open_Pad1.0x1.5mm
R23, R24: 96; R_0603_1608Metric
U4: MCP2561/2FD; SOIC-8_3.9x4.9mm_P1.27mm

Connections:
+5V: C12.1, JP1.1 (A), U4.3 (VDD); also elsewhere on the board
/CAN/CAN_H: U4.7 (CANH); also elsewhere on the board
/CAN/CAN_L: U4.6 (CANL); also elsewhere on the board
/CAN/CAN_RX: D14.2 (A), U4.4 (RXD); also elsewhere on the board
/CAN/CAN_TX: D13.2 (A), U4.1 (TXD); also elsewhere on the board
GNDD: C12.2, R23.2, R24.2, U4.2 (VSS), U4.8 (STBY); also elsewhere on the board
unnamed: D13.1 (K), R23.1
unnamed: D14.1 (K), R24.1
unnamed: JP1.2 (B), U4.5 (VIO)

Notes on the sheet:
MCP2562FDを使うならジャンパする
Vcc = 3.3V Vf = 2.1V, If = 12.5mA (3.3-2.1) / 0.0125 = 96Ω



Board: 2 copper layers, 70.0 x 45.0 mm, 89 parts (11 on the bottom side), 71 nets.

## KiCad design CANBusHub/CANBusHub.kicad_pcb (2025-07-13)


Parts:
D1: PWR; LED_0603_1608Metric
H1, H2, H3, H4, H5: MountingHole_Pad; MountingHole_3.2mm_M3_Pad
H6: MountingHole; Title
H7: MountingHole; Info_M
J1: CAN1_IN; PAコネクタ(4ピンサイド型)
J2: CAN2_IN; PAコネクタ(4ピンサイド型)
J3: CAN_OUT1; IDC-Header_2x03_P2.54mm_Vertical
J4: CAN_OUT2; IDC-Header_2x03_P2.54mm_Vertical
J5: CAN_OUT3; IDC-Header_2x03_P2.54mm_Vertical
J6: CAN_OUT4; IDC-Header_2x03_P2.54mm_Vertical
J7: CAN1_OUT; PAコネクタ(4ピンサイド型)
J8: CAN2_OUT; PAコネクタ(4ピンサイド型)
J11: PWR_IN; USB_C_Receptacle_GCT_USB4125-xx-x_6P_TopMnt_Horizontal
R1: 430; R_0603_1608Metric
R2, R3: 5.1k; R_0603_1608Metric
SW1, SW2, SW3, SW4: CAN1/2; SLW
SW5, SW6, SW7, SW8: SW_DPDT_x2; SLW

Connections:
+5VD: D1.2 (A), J1.1, J2.1, J3.5, J3.6, J4.5, J4.6, J5.5, J5.6, J6.5, J6.6, J7.1, J8.1, J11.A9 (VBUS), J11.B9 (VBUS)
/CAN1_H: J1.2, J7.2, SW1.3 (C), SW2.3 (C), SW3.3 (C), SW4.3 (C), SW5.1 (A), SW6.1 (A), SW7.1 (A), SW8.1 (A)
/CAN1_L: J1.3, J7.3, SW1.6 (C), SW2.6 (C), SW3.6 (C), SW4.6 (C), SW5.4 (A), SW6.4 (A), SW7.4 (A), SW8.4 (A)
/CAN2_H: J2.2, J8.2, SW1.1 (A), SW2.1 (A), SW3.1 (A), SW4.1 (A), SW5.3 (C), SW6.3 (C), SW7.3 (C), SW8.3 (C)
/CAN2_L: J2.3, J8.3, SW1.4 (A), SW2.4 (A), SW3.4 (A), SW4.4 (A), SW5.6 (C), SW6.6 (C), SW7.6 (C), SW8.6 (C)
GNDD: H1.1, H2.1, H3.1, H4.1, H5.1, J1.4, J2.4, J3.1, J3.2, J4.1, J4.2, J5.1, J5.2, J6.1, J6.2, J7.4, J8.4, J11.A12 (GND), J11.B12 (GND), R1.2, R2.2, R3.2
unnamed: D1.1 (K), R1.1
unnamed: J3.3, SW1.2 (B), SW5.2 (B)
unnamed: J3.4, SW1.5 (B), SW5.5 (B)
unnamed: J4.3, SW2.2 (B), SW6.2 (B)
unnamed: J4.4, SW2.5 (B), SW6.5 (B)
unnamed: J5.3, SW3.2 (B), SW7.2 (B)
unnamed: J5.4, SW3.5 (B), SW7.5 (B)
unnamed: J6.3, SW4.2 (B), SW8.2 (B)
unnamed: J6.4, SW4.5 (B), SW8.5 (B)
unnamed: J11.A5 (CC1), R3.1
unnamed: J11.B5 (CC2), R2.1



Board: 2 copper layers, 100.0 x 57.0 mm, 28 parts (10 on the bottom side), 17 nets.

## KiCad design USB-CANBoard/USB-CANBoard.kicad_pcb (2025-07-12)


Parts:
C1, C2, C7, C13: 4.7u; C_0603_1608Metric
C3, C4, C5, C6, C8, C12, C14, C15, C16, C17, C18: 0.1u; C_0603_1608Metric
C9: 1u; C_0603_1608Metric
C10, C11: 12p; C_0603_1608Metric
D1, D2, D5: LED; LED_0603_1608Metric
D3, D4: D; Nexperia_CFP3_SOD-123W
D6: CAN1_TX; LED_0603_1608Metric
D7: CAN1_RX; LED_0603_1608Metric
D8: CAN2_TX; LED_0603_1608Metric
D9: CAN2_RX; LED_0603_1608Metric
D10, D11: CAN_R; LED_0603_1608Metric
F1, F2: Polyfuse; MF-FSMF
FB1: FerriteBead; L_0603_1608Metric
H1, H2, H3, H4: MountingHole_Pad; MountingHole_3.2mm_M3_Pad
H5: MountingHole; Title
H6: MountingHole; Aho_old_M
H7: MountingHole; Aho_new_M
H8: MountingHole; Info_M
J1: USB_FS; USB_C_Receptacle_GCT_USB4105-xx-A_16P_TopMnt_Horizontal
J2: DEBUG; USB_C_Receptacle_GCT_USB4105-xx-A_16P_TopMnt_Horizontal
J3: CAN1; PAコネクタ(4ピンサイド型)
J4: CAN2; PAコネクタ(4ピンサイド型)
J5: SWD; JST_SH_SM04B-SRSS-TB_1x04-1MP_P1.00mm_Horizontal
R1, R2: 430; R_0603_1608Metric
R3: 10k; R_0603_1608Metric
R4: 10k; R_0603_1608Metric; not fitted
R5, R6, R7, R8: 5.1k; R_0603_1608Metric
R9, R10, R11, R12, R13: 96; R_0603_1608Metric
R14, R16: 120; R_0603_1608Metric
R15, R17: 420; R_0603_1608Metric
R18: 100; R_0603_1608Metric
R19: 600; R_0603_1608Metric
R20: 300; R_0603_1608Metric
SW1: RESET; TVAF06-A020B-R
SW2, SW3: CAN_R; SLW
U1: STM32F446RETx; LQFP-64_10x10mm_P0.5mm
U2: TLV1117-33; SOT-223-3_TabPin2
U3: CH340E; MSOP-10_3x3mm_P0.5mm
U4, U5: ISO1044BD; SOIC-8_3.9x4.9mm_P1.27mm
U6: LED_GRB; LED_ROHM_SMLVN6
Y1: 26MHz; XRCGB

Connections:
+3.3V: C2.1, C3.1, C4.1, C5.1, C6.1, C7.1, C14.1, FB1.1, R4.1, U1.1 (VBAT), U1.19 (VDD), U1.32 (VDD), U1.48 (VDD), U1.64 (VDD), U2.2 (VO), U3.7 (VCC), U3.10 (V3)
+3.3VADC: C8.1, C9.1, FB1.2, U1.13 (VDDA)
+5V: C1.1, C15.2, C17.2, D1.2 (A), D3.1 (K), D4.1 (K), U2.3 (VI), U4.1 (VCC1), U5.1 (VCC1)
+5VD: C16.2, C18.2, D2.2 (A), D10.2 (A), D11.2 (A), J3.1, J4.1, U4.8 (VCC2), U5.8 (VCC2)
/NRST: C12.1, J5.4, SW1.2, U1.7 (NRST)
/SWCLK: J5.2, U1.49 (PA14)
/SWDIO: J5.1, U1.46 (PA13)
CAN1_RX: D7.2 (A), U1.61 (PB8), U4.3 (RXD)
CAN1_TX: D6.2 (A), U1.62 (PB9), U4.2 (TXD)
CAN2_RX: D9.2 (A), U1.57 (PB5), U5.3 (RXD)
CAN2_TX: D8.2 (A), U1.58 (PB6), U5.2 (TXD)
GND: C1.2, C2.2, C3.2, C4.2, C5.2, C6.2, C7.2, C8.2, C9.2, C10.2, C11.2, C12.2, C13.2, C14.2, C15.1, C17.1, H1.1, H2.1, J1.A1 (GND), J1.A12 (GND), J1.B1 (GND), J1.B12 (GND), J2.A1 (GND), J2.A12 (GND), J2.B1 (GND), J2.B12 (GND), J5.3, R1.2, R3.2, R5.2, R6.2, R7.2, R8.2, R9.2, R10.2, R11.2, R12.2, R13.2, SW1.1, U1.12 (VSSA), U1.18 (VSS), U1.31 (VSS), U1.47 (VSS), U1.63 (VSS), U2.1 (GND), U3.3 (GND), U4.4 (GND1), U5.4 (GND1), U6.4, U6.5, U6.6
GNDD: C16.1, C18.1, H3.1, H4.1, J3.4, J4.4, R2.2, SW2.6 (C), SW3.6 (C), U4.7 (GND2), U5.7 (GND2)
LED_B: R18.2, U1.41 (PA8)
LED_G: R20.2, U1.43 (PA10)
LED_R: R19.2, U1.42 (PA9)
unnamed: D1.1 (K), R1.1
unnamed: D2.1 (K), R2.1
unnamed: D3.2 (A), F1.1
unnamed: D4.2 (A), F2.1
unnamed: D5.2 (A), U3.6 (TNOW)
unnamed: D5.1 (K), R9.1
unnamed: D6.1 (K), R10.1
unnamed: D7.1 (K), R11.1
unnamed: D8.1 (K), R12.1
unnamed: D9.1 (K), R13.1
unnamed: D10.1 (K), R15.1
unnamed: D11.1 (K), R17.1
unnamed: F1.2, J1.A4 (VBUS), J1.A9 (VBUS), J1.B4 (VBUS), J1.B9 (VBUS)
unnamed: F2.2, J2.A4 (VBUS), J2.A9 (VBUS), J2.B4 (VBUS), J2.B9 (VBUS)
unnamed: J1.A5 (CC1), R6.1
unnamed: J1.B5 (CC2), R5.1
unnamed: J2.A5 (CC1), R8.1
unnamed: J2.B5 (CC2), R7.1
unnamed: J3.2, SW2.1 (A), U4.6 (CANH)
unnamed: J3.3, R14.1, U4.5 (CANL)
unnamed: J4.2, SW3.1 (A), U5.6 (CANH)
unnamed: J4.3, R16.1, U5.5 (CANL)
unnamed: R18.1, U6.1
unnamed: R19.1, U6.2
unnamed: R20.1, U6.3
unnamed: R14.2, SW2.2 (B)
unnamed: R15.2, SW2.5 (B)
unnamed: R16.2, SW3.2 (B)
unnamed: R17.2, SW3.5 (B)
unnamed: R3.1, R4.2, U1.60 (BOOT0)
unnamed: C10.1, U1.5 (PH0), Y1.1
unnamed: C11.1, U1.6 (PH1), Y1.3
unnamed: C13.1, U1.30 (VCAP_1)
unnamed: J2.A6 (D+), J2.B6 (D+), U3.1 (UD+)
unnamed: J2.A7 (D-), J2.B7 (D-), U3.2 (UD-)
UART2_RX: U1.17 (PA3), U3.8 (TXD)
UART2_TX: U1.16 (PA2), U3.9 (RXD)
USB_D+: J1.A6 (D+), J1.B6 (D+), U1.45 (PA12)
USB_D-: J1.A7 (D-), J1.B7 (D-), U1.44 (PA11)



Board: 2 copper layers, 60.0 x 40.0 mm, 75 parts (21 on the bottom side), 55 nets.

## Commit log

2025-03-19 GPIO Board ver1.0
    [CAN.kicad_sch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]
2025-03-19 バックアップファイルを追跡対象から除外
2025-04-01 XT30 Hub ver1.0
    [XT30Hub.kicad_pcb, XT30Hub.kicad_sch, bom.csv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]
2025-04-07 XT60 Hub ver1.0
    [XT60Hub.kicad_pcb, XT60Hub.kicad_sch, bom.csv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]
2025-04-07 [XT30Hub] : 裏面の枠線の太さを修正
    [XT30Hub.kicad_pcb, bom.csv, positions.csv]
2025-04-07 [XT30Hub] : 回路図をPDF化
    [XT30Hub.kicad_sch]
2025-04-07 [XT60Hub] : ガーバーファイルを追加
2025-04-07 [GPIOBoard] : 回路図の一時ファイルを削除
2025-04-12 GPIO Board ver1.1
    [CAN.kicad_sch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]
2025-04-12 PWM Board ver1.0
    [CAN.kicad_sch, Isolator.kicad_sch, MCU.kicad_sch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]
2025-04-12 RoboMaster Board ver1.0
    [CAN1.kicad_sch, CAN2.kicad_sch, MCU.kicad_sch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]
2025-04-12 Solenoid Driver ver1.0
    [CAN.kicad_sch, Isolator.kicad_sch, MCU.kicad_sch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]
2025-04-12 [XT30Hub] : 発注前に最終調整
    [XT30Hub.kicad_pcb]
2025-04-12 [XT30Hub] : 基板の画像を追加
2025-04-12 [XT60Hub] : 発注前に最終調整
    [XT60Hub.kicad_pcb, bom.csv, positions.csv]
2025-04-12 [XT60Hub] : 基板の画像を追加
2025-04-13 [GPIOBoard] : 基板の表面と裏面の画像を追加
2025-04-13 [GPIOBoard] : README に説明や画像などを追加
2025-04-13 [GPIOBoard] : 不要な画像を削除
2025-04-13 [PWMBoard] : 基板の表面と裏面の画像を追加
2025-04-13 [GPIOBoard] : 基板の画像をレイトレーシング画像に変更
2025-04-13 [PWMBoard] : 基板の画像をレイトレーシング画像に変更
2025-04-13 [PWMBoard] : 不要な画像を削除
2025-04-13 [PWMBoard] : README を追加
2025-04-13 [RoboMasterBoard] : 基板の画像をレイトレーシング画像に変更
2025-04-13 [RoboMasterBoard] : README を追加
2025-04-13 [SolenoidDriver] : 基板の画像をレイトレーシング画像に変更
2025-04-13 [SolenoidDriver] : README を追加
2025-04-13 [XT30Hub] : 基板の画像をレイトレーシング画像に変更
2025-04-13 [XT30Hub] : README を追加
2025-04-13 [XT60Hub] : 基板の画像をレイトレーシング画像に変更
2025-04-13 [XT60Hub] : README を追加
2025-05-01 Motor Driver ver1.0
    [MotorDriver.csv, MotorDriver.kicad_pcb, MotorDriver.kicad_sch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]
2025-06-01 CAN Bus Hub ver1.0
    [CANBusHub.csv, CANBusHub.kicad_pcb, CANBusHub.kicad_sch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]
2025-06-01 Converter Board ver1.0
    [ConverterBoard.csv, ConverterBoard.kicad_pcb, ConverterBoard.kicad_sch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]
2025-06-01 Power Board ver1.0
    [PowerBoard.csv, PowerBoard.kicad_pcb, PowerBoard.kicad_sch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]
2025-06-01 Remote Emergency Stop Board RX ver1.0
    [RemoteEmergencyStopBoard_RX.csv, RemoteEmergencyStopBoard_RX.kicad_pcb, RemoteEmergencyStopBoard_RX.kicad_sch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]
2025-06-01 Remote Emergency Stop Board TX ver1.0
    [RemoteEmergencyStopBoard_TX.csv, RemoteEmergencyStopBoard_TX.kicad_pcb, RemoteEmergencyStopBoard_TX.kicad_sch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]
2025-06-17 Converter Board ver1.1
    [ConverterBoard.kicad_pcb, ConverterBoard.kicad_sch, bom.csv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]
2025-06-17 [Converter Board] : 基板上の日付を修正
    [ConverterBoard.kicad_pcb]
2025-07-01 GPIO Board ver1.2
    [GPIOBoard.csv, GPIOBoard.kicad_pcb, GPIOBoard.kicad_sch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]
2025-07-01 PWM Board ver1.1
    [PWMBoard.csv, PWMBoard.kicad_pcb, PWMBoard.kicad_sch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]
2025-07-01 Solenoid Driver ver1.1
    [SolenoidDriver.csv, SolenoidDriver.kicad_pcb, SolenoidDriver.kicad_sch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]
2025-07-01 RoboMaster Board ver1.1
    [RoboMasterBoard.csv, RoboMasterBoard.kicad_pcb, RoboMasterBoard.kicad_sch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]
2025-07-01 [PWM Board] : 日付の説明を変更
2025-07-05 .kicad_prl を追跡対象から除外
2025-07-12 USB-CAN Board ver1.0
    [USB-CANBoard.csv, USB-CANBoard.kicad_pcb, USB-CANBoard.kicad_sch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]
2025-07-12 Motor Driver ver2.0
    [MotorDriver.csv, MotorDriver.kicad_pcb, MotorDriver.kicad_sch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]
2025-07-12 コンデンサの容量を修正
    [RoboMasterBoard_MCU.kicad_sch]
2025-07-12 ファームウェアのリポジトリへのリンクと各基板の説明を追加
2025-07-13 CAN Bus Hub ver1.1
    [CANBusHub.kicad_pcb, CANBusHub.kicad_sch, CANBusHub.xlsx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]
2025-07-13 Board Fixer ver1.0
    [base.SLDPRT, base.STL, base1.STL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]
2025-07-14 [Board Base] : 名前を変更
2025-07-15 [Board Base] : 不要なモデルを削除
    [base.SLDPRT, cap.SLDPRT, slide1.SLDPRT]
2025-07-15 基板の3Dモデルを別のフォルダに移動
2025-07-15 GPIO Board ver1.3
    [GPIOBoard.kicad_pcb, GPIOBoard.kicad_sch, GPIOBoard_CAN.kicad_sch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]
2025-07-16 各基板の3Dモデルを追加
2025-07-17 CAN Bus Hub の3Dモデルを更新
2025-07-17 Board Base ver2.0
    [base.SLDPRT, base_cap.SLDPRT, base_x4.SLDPRT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]
2025-07-17 [Board Base] : 画像を追加
2025-08-19 Motor Driver ver2.1
    [MotorDriver.kicad_pcb, MotorDriver.kicad_sch, MotorDriver.xlsx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]
2025-09-07 Fan Board ver1.0
    [FanBoard.kicad_pcb, FanBoard.kicad_sch, bom.csv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]
2025-09-12 Converter Board ver1.2
    [ConverterBoard.csv, ConverterBoard.kicad_pcb, ConverterBoard.kicad_sch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]
2025-09-12 XT30 Hub ver1.1
    [XT30Hub.kicad_pcb, XT30Hub.kicad_sch]
2025-09-12 XT60 Hub ver1.1
    [XT60Hub.kicad_pcb, XT60Hub.kicad_sch, positions.csv]
2025-09-27 LED Board ver1.0
    [LEDBoard.kicad_pcb, LEDBoard.kicad_sch, bom.csv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]
2026-03-16 説明文を変更
